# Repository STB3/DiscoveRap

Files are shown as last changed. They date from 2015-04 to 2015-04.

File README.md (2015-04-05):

# DiscoveRap
RpRap Electronics Expansion Board for the STM32F429 Discovery Board<p>
Max. 3 Extruders, X, Y, Z Axis<br>
Heated Bed<br>
Case Fan & Light<br>
Fans for each Extruder<br>
TMC260 Stepper driver<br>
USB-OTG, USB-Virtual COM, SD-Card Storage<br>
WLAN option<br>
Needs the STM32F429 Demoboard for operation<br>

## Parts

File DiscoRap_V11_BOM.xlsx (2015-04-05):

Bill of Material for DiscoRap V1.1
Qty | Value | Tolerance | Voltage | Other | Device | Package | Parts | Description | Manufacturer | Manufacturer Part No. | Mouser | Digikey
11 | Green |  |  | standard 10..20mA | LED | 0805 | LED401, LED501, LED502, LED503, LED504, LED601, LED602, LED603, LED604, LED605, LED801 | LED
6 | Molex Serie 6373 |  |  |  | M02POLAR | MOLEX-1X2 | JP704, JP706, JP709, JP710, JP711, JP902 | Molex Serie 6373 | Molex | 22-23-2021 | 538-22-23-2021
11 | Molex Serie 6373 |  |  |  | M03POLAR | MOLEX-1X3 | JP601, JP602, JP603, JP604, JP605, JP701, JP702, JP703, JP705, JP707, JP708 | Molex Serie 6373 | Molex | 22-23-2031 | 538-22-23-2031
2 |  |  |  |  | Pinheader 1x2 | RM 2.54mm | JP101, JP102 | PIN HEADER
1 |  |  |  |  | Pinheader 2x3 | RM 2.54mm | JP901 | PIN HEADER
1 |  |  |  |  | Pinheader 2x5 | RM 2.54mm | JP103 | PIN HEADER
3 |  |  |  |  | Screw Clamp 2 pol. | RM5.00 | X501, X502, X503 | Screw Clamp | Phoenix Contact | 1935161 | 651-1935161
8 |  |  |  |  | Screw Clamp 4 pol. | W237-4 | X201, X202, X203, X301, X302, X303, X401, X802 | Screw Clamp | Phoenix Contact | 1935187 | 651-1935187
0 | n.c. |  |  | not populated | Resistor | 2512 | R801 | Resistor
12 | 0R15 | 1% |  | 500mW | Resistor | 1206 | R201, R202, R203, R204, R205, R206, R301, R302, R303, R304, R305, R306 | Resistor | Panasonic | ERJ-8BSFR15V | 667-ERJ-8BSFR15V
9 | 100 | 5% |  |  | Resistor | 0805 | R402, R504, R505, R509, R603, R604, R608, R610, R614
1 | 1000uF | 20% | min. 30V |  | Electrolytic Capacitor | RM 5mm / Diameter < 11.5mm | C801 | Electrolytic Capacitor
9 | 100k | 5% |  |  | Resistor | 0805 | R401, R502, R503, R508, R601, R602, R607, R609, R613 | Resistor
7 | 100nF | 10% | min. 25V | X7R | Capacitor | 0805 | C101, C102, C103, C104, C401, C813, C814 | Capacitor
18 | 100nF |  | min. 50V | X7R | Capacitor | 0805 | C203, C204, C207, C208, C209, C211, C224, C226, C227, C303, C304, C307, C308, C309, C311, C324, C326, C327 | Capacitor
24 | 100p |  | min. 63V | NP0 | Capacitor | 0805 | C210, C212, C213, C214, C215, C216, C219, C220, C228, C229, C230, C232, C310, C312, C313, C314, C315, C316, C319, C320, C328, C329, C330, C332 | Capacitor
7 | 10k |  |  |  | Resistor | 0805 | R101, R102, R103, R104, R105, R106, R107 | Resistor
2 | 10k2 | 1% |  |  | Resistor | 0805 | R806, R808 | Resistor
1 | 10nF |  | min. 30V | X7R | Capacitor | 0805 | C809 | Capacitor
2 | 10µ | 10% | 6.3V | X5R | Capacitor | 0805 | C815, C817 | Capacitor | AVX | 08056D106KAT2A | 581-08056D106K
1 | 20k | 1% |  |  | Resistor | 0805 | R805 | Resistor
6 | 220nF | 10% | min. 16V |  | Capacitor | 0805 | C205, C206, C225, C305, C306, C325 | Capacitor
1 | 22n | 10% | min. 16V |  | Capacitor | 0805 | C812 | Capacitor
12 | 22µF | 20% | min. 35V | Ripple current >150mA | Electrolytic Capacitor | SMD B6 (6.3 x 5.3 mm²) | C217, C218, C221, C222, C231, C233, C317, C318, C321, C322, C331, C333 | Electrolytic Capacitor | KEMET | EEV226M035A9DAA | 80-EEV226M035A9DAA
1 | 8kBit serial eePROM |  |  |  | eePROM | SOT23-5L | IC102 | Serial EEPROM | Microchip | 24LC08BT-I/OT | 579-24LC08BT-I/OT
5 | 2k2 | 1% |  |  | Resistor | 0805 | R705, R710, R714, R715, R716 | Resistor
11 | 2k7 | 5% |  |  | Resistor | 0805 | R403, R501, R506, R507, R510, R605, R606, R611, R612, R615, R802 | Resistor
2 | 2n7 | 10% |  |  | Capacitor | 0805 | C802, C810 | Capacitor
1 | 2u2 | 20% | min. 16V |  | Capacitor | 0805 | C402 | Capacitor
1 | 330p | 10% |  |  | Capacitor | 0805 | C807 | Capacitor
1 | 3k24 | 1% |  |  | Resistor | 0805 | R807 | Resistor
3 | 3k3 | 5% |  |  | Resistor | 0805 | R901, R902, R903 | Resistor
1 | 3n3 | 10% |  |  | Capacitor | 0805 | C811 | Capacitor
16 | 470nF | 10% | min. 10V |  | Capacitor | 0805 | C201, C202, C223, C301, C302, C323, C701, C705, C706, C710, C711, C712, C713, C714, C715, C716 | Capacitor
1 | 47p | 10% |  |  | Capacitor | 0805 | C808 | Capacitor
6 | 4k7 | 5% |  |  | Resistor | 0805 | R701, R702, R703, R706, R707, R708 | Resistor
1 | 4k87 | 1% |  |  | Resistor | 0805 | R804 | Resistor
15 | 4n7 | 10% | min. 35V |  | Capacitor | 0805 | C403, C501, C502, C503, C601, C602, C603, C604, C605, C702, C703, C704, C707, C708, C709 | Capacitor
6 | 4µ7 | 20% | min. 25V | X5R | Capacitor | 0805 | C803, C804, C805, C806, C816, C818 | Capacitor | AVX | 08053D475MAT2A | 581-08053D475MAT2A
5 | 6k8 | 5% |  |  | Resistor | 0805 | R704, R709, R711, R712, R713 | Resistor
1 | 820 | 1% |  |  | Resistor | 0805 | R809 | Resistor
1 | 82k |  |  |  | Resistor | 0805 | R803 | Resistor
1 | AMP_1010070864 |  |  |  | AMP_1010070864 | AMP_1010070864 | X103 | Amphenol SD-Card Connector |  | 1010070864 | 523-101-00708-64
0 | n.c. |  |  | not populated | ATX-4VERTICAL | MINIFITJR-4-VERTICAL | X801
2 | B240A-13-F |  |  |  | Schottky Diode | SMA | D802, D803 | Surface Mount Schottky Power Rectifier | Diodes Inc. | B240A-13-F | 621-B240A-F
2 | BC817-25 |  |  |  | Transistor NPN | SOT23-BEC | Q101, Q102 | NPN Transistor
1 | BZX84C15 |  |  |  | Zener Diode 15V | TO236 | D801 | Zener Diode 15V | Fairchild | BZX84C15
4 | S1G-E3/5AT |  |  |  | Rectifier Diode | SMA | D401, D501, D502, D503 | Rectifier Diode | Vishay | S1G-E3/5AT | 625-S1G-E3/5AT
1 | DG2722 |  |  |  | USB Switch | MINI_QFN_10L | IC101 | USB Switch | Vishay | DG2722DN-T1-E4 | 781-DG2722DN-E4
1 | Buzzer |  | 3.3V |  | Buzzer | RM4 / RM7.6 | BUZ1 | Buzzer | Mallory | PB-09N23P-03Q | 539-PB09N23P-03Q
4 | FUSE3557 |  |  |  | Fuseholder | 3557 | F501, F801 | Fuseholder | Keystone Electronics | 3557 | 534-3557
1 | MCP1402 |  |  |  | MCP1402 | SOT23-5L | IC401 | MOSFET driver | Microchip | MCP1402T-E/OT | 579-MCP1402T-E/OT
2 | MCP23S17SO |  |  |  | MCP23S17SO | SO28W | IC103, IC104 | SPI Port Expander | Microchip | MCP23S17T-E/SO | 579-MCP23S17T-E/SO
1 | SI7145DP |  |  |  | SI7145DP | SO-8_POWERPACK | T801 | P-Ch. MOSFET 2.6mOhm -30V | Vishay | SI7145DP-T1-GE3 | 781-SI7145DP-GE3
8 | SIA400EDJ |  |  |  | SIA400EDJ | SC70-6L | T501, T502, T503, T601, T602, T603, T604, T605 | N-Ch. MOSFET 19mOhm 30V | Vishay | SIA400EDJ-T1-GE3 | 78-SIA400EDJ-T1-GE3
1 | SIR416DP |  |  |  | SIR416DP | SO-8_POWERPACK | T401 | N-Ch. MOSFET 3.8mOhm 40V | Vishay | SIR416DP-GE3 | 781-SIR416DP-GE3
1 | SRN8040-150M |  |  |  | SRN8040 | SRN8040 | L803 | Bourns Power Inductors 15uH/2.4A |  | SRN8040-150M | 652-SRN8040-150M
2 | SRN8040-220M |  |  |  | SRN8040 | SRN8040 | L801, L802 | Bourns Power Inductors 22uH/2.4A |  | SRN8040-220M | 652-SRN8040-220M
2 | Pfostenbuchse | solder side ! |  |  | 32x2 | RM 2.54mm
2 | Pfostenbuchse | solder side ! |  |  | 1x2 | RM 2.54mm
1 | TE_292303-9 |  |  |  | TE_292303-9 | TE_USB_A_SMD | X102 | TE Connectivity USB-A | TE Connectivity | 292303-9 | 571-292303-9
6 | TMC260 |  |  |  | TMC260 | SQFP-S-10X10-44 | IC201, IC202, IC203, IC301, IC302, IC303 | Stepper Driver | Trinamic | TMC260-PA-T |  | 1460-1070-1-ND
2 | TPS54332 |  |  |  | TPS54332 | PDSO-G8 | IC801, IC802 | TPS54332 | Texas Instruments | TPS54332DDAR | 595-TPS54332DDAR
1 | USB-B_SMD |  |  |  | USB-B_SMD | USB_B_SMD | X101 |  |  | KUSBEX-SMT-BS1N-BTR | 806-KUSBEXSMTBS1NBTR
 | Changes | Date | Vers. | Author
 | Initial Version | 29.03.2015 | 1.1 | DE

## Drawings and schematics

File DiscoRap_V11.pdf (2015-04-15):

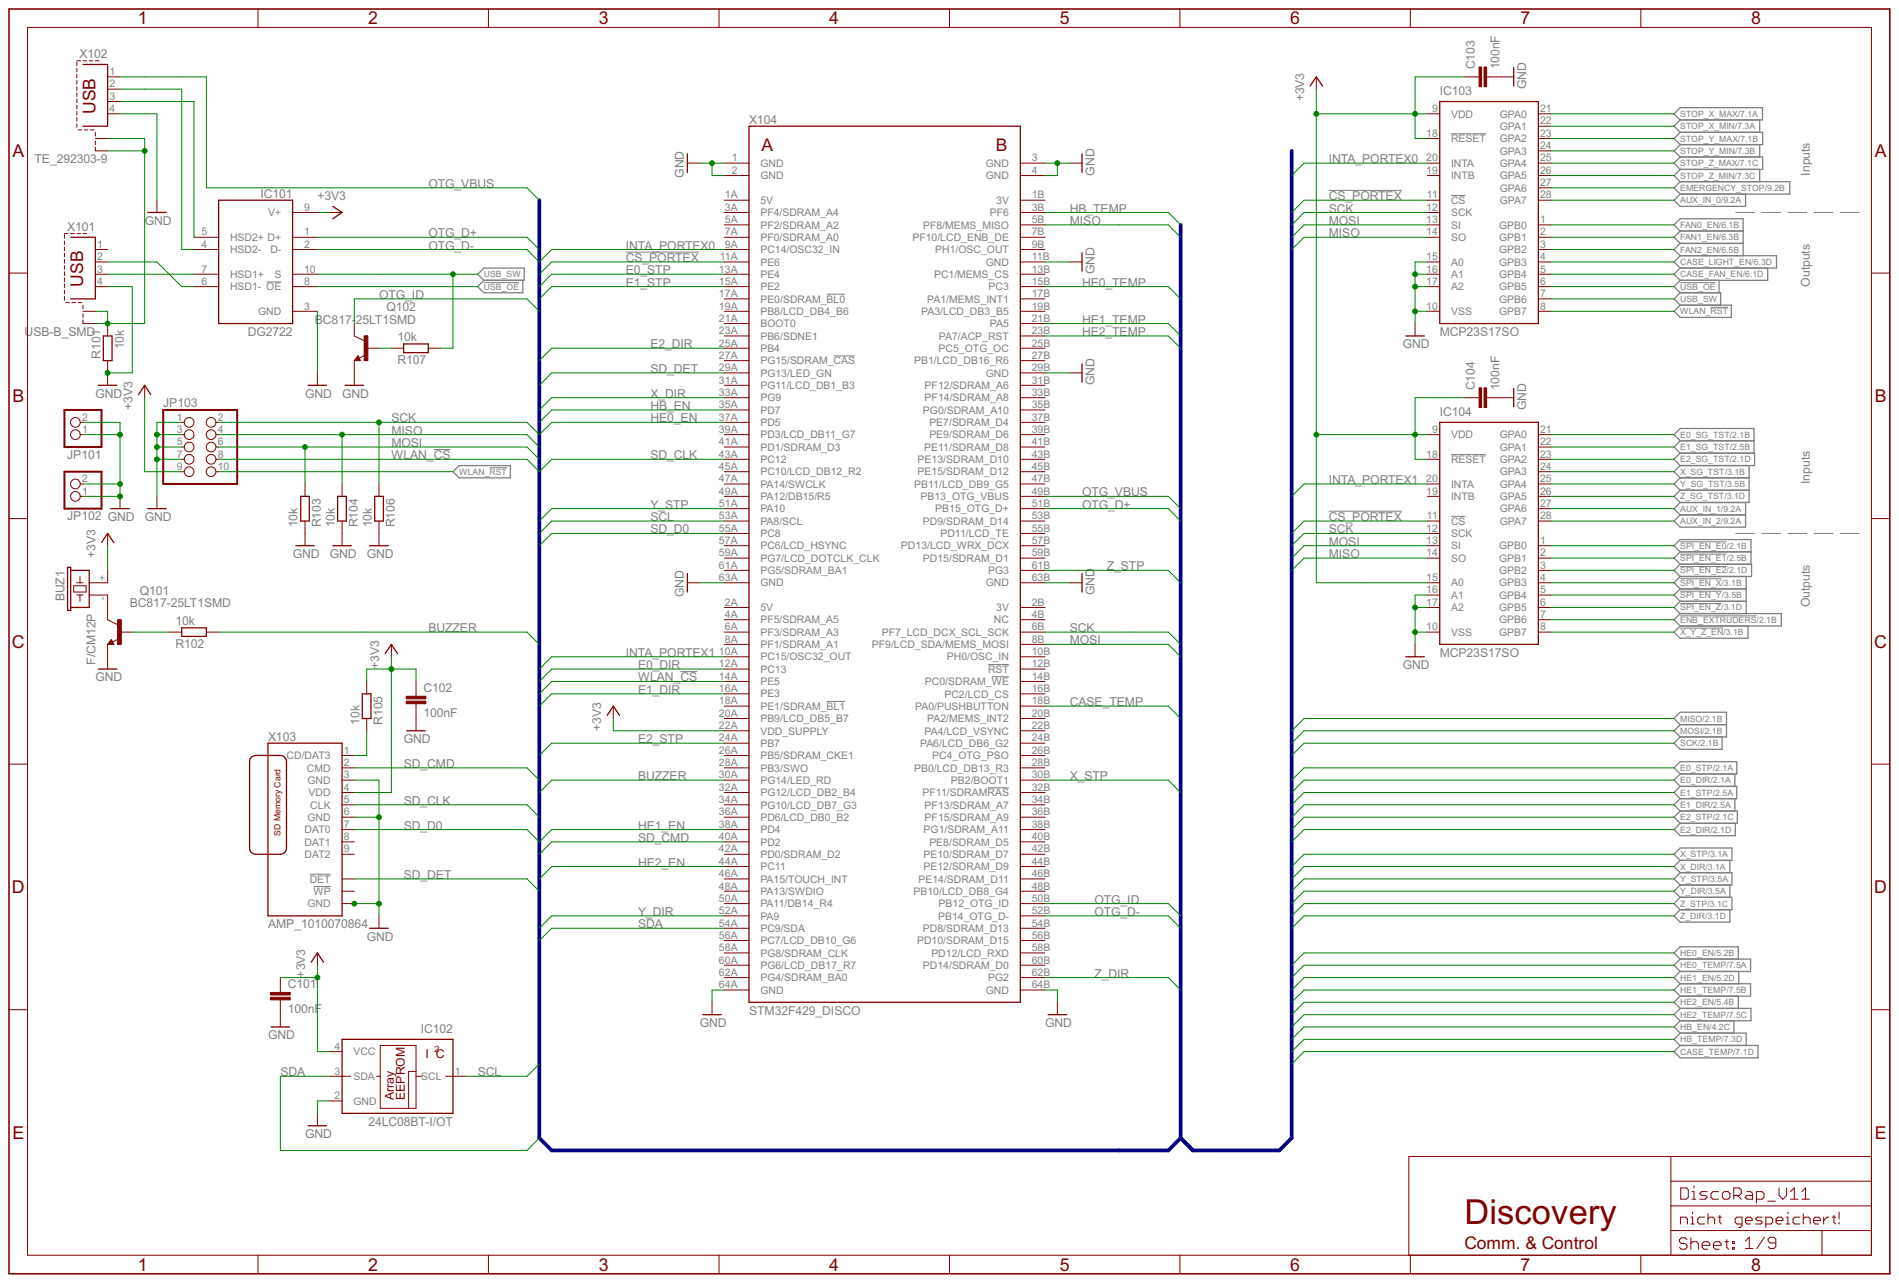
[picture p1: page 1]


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

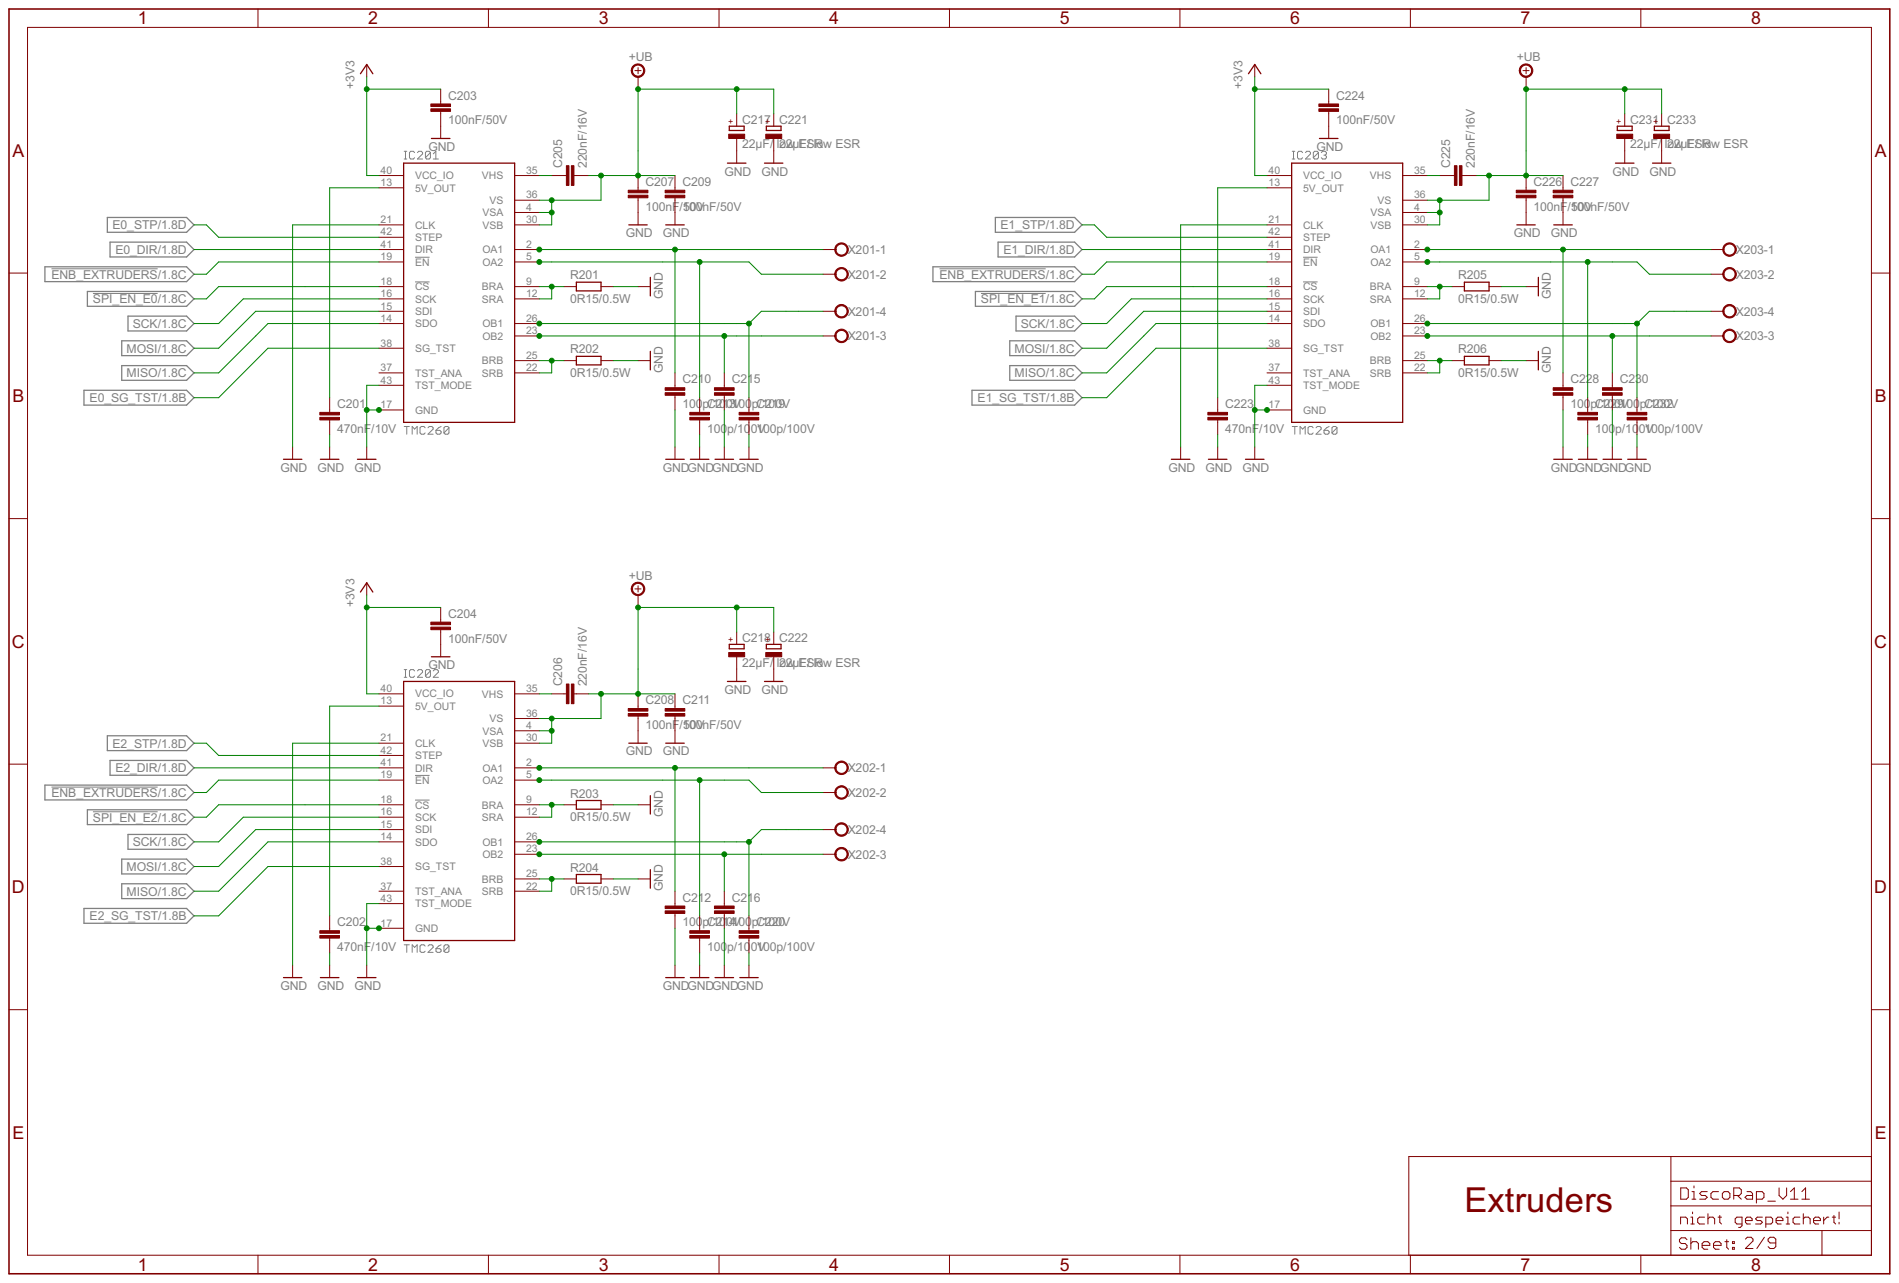
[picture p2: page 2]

22µF/ l2o2wµEFS/ lRow ESR GND GND

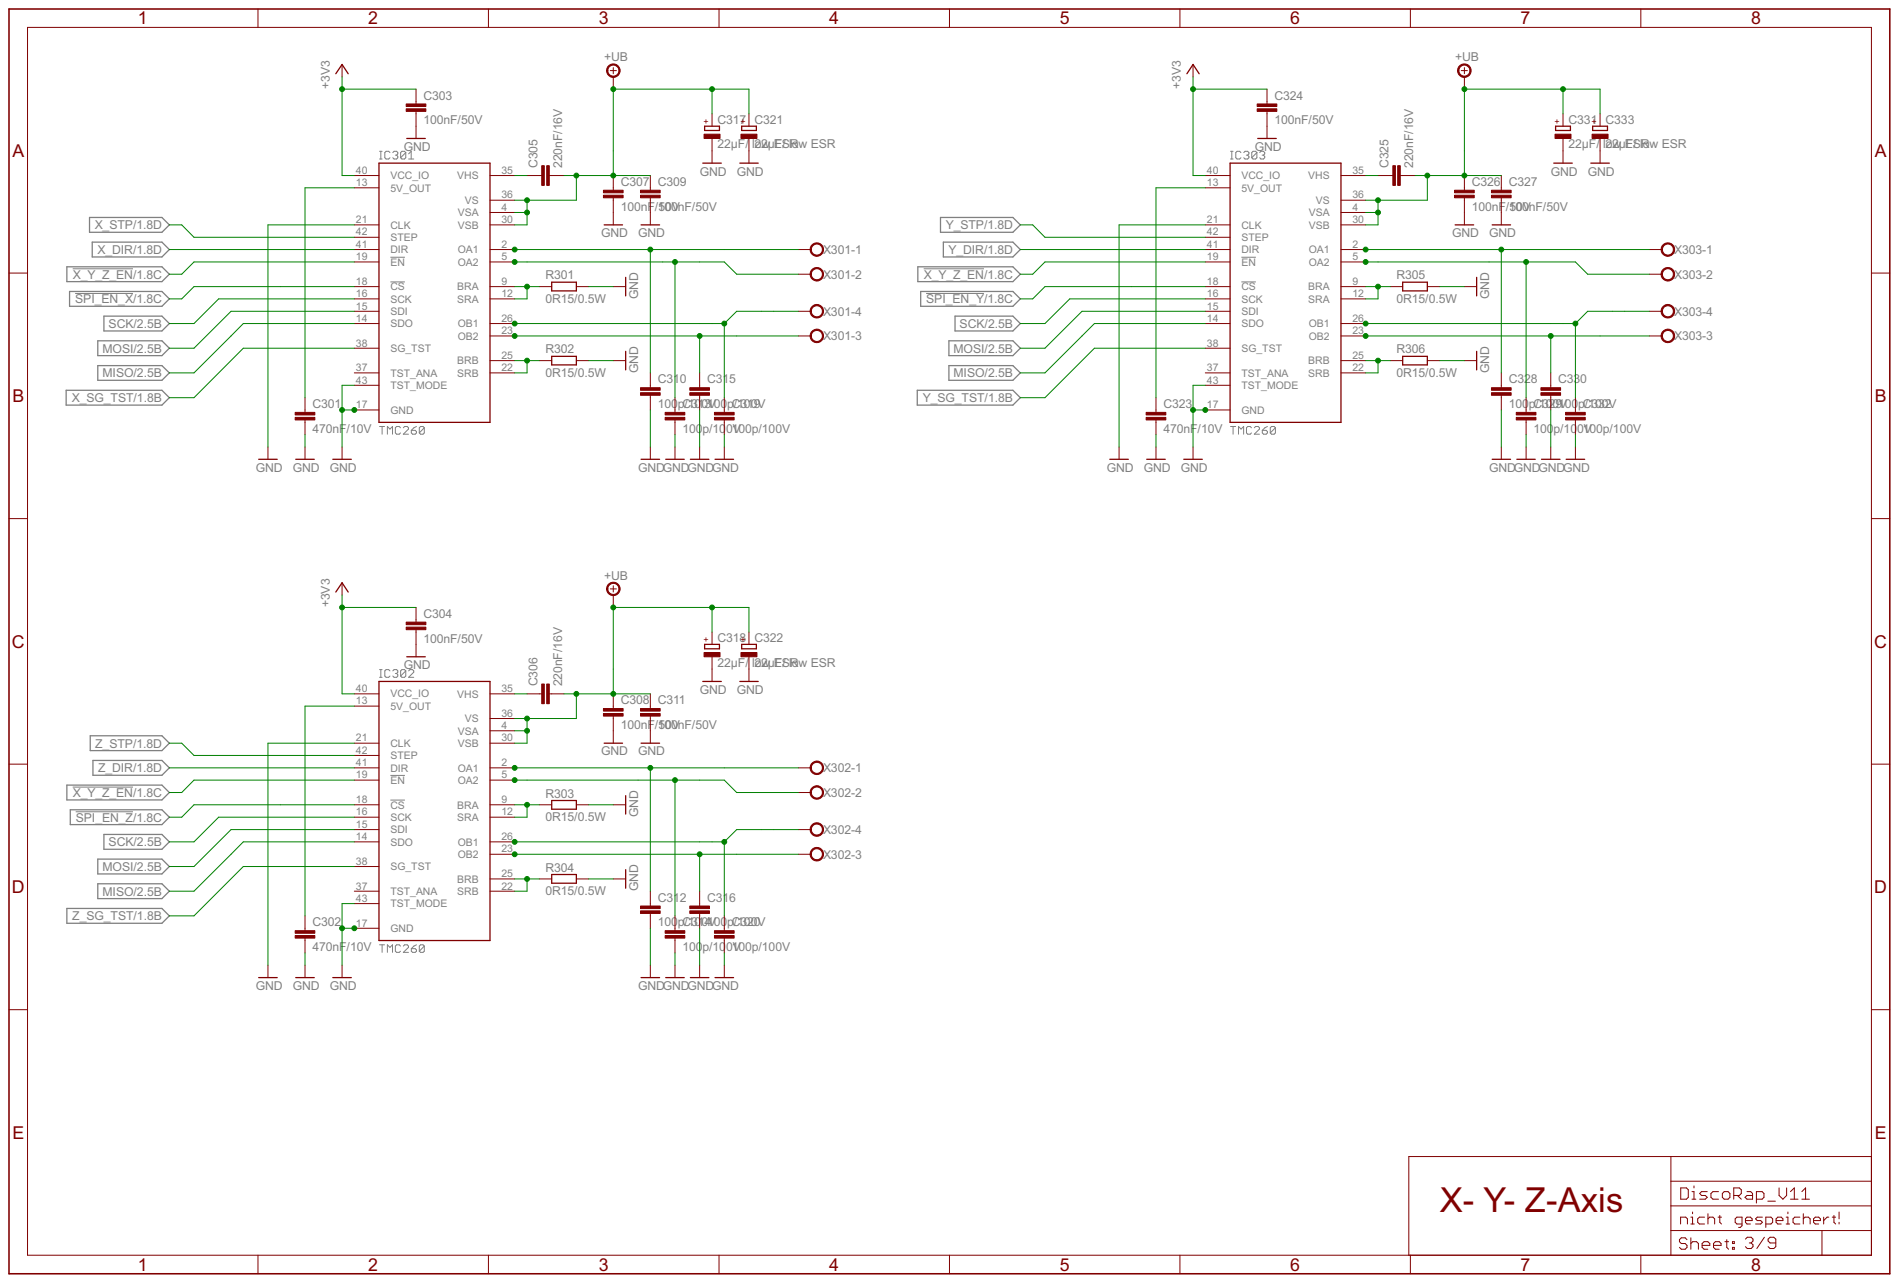
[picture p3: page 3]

22µF/ l2o2wµEFS/ lRow ESR GND GND

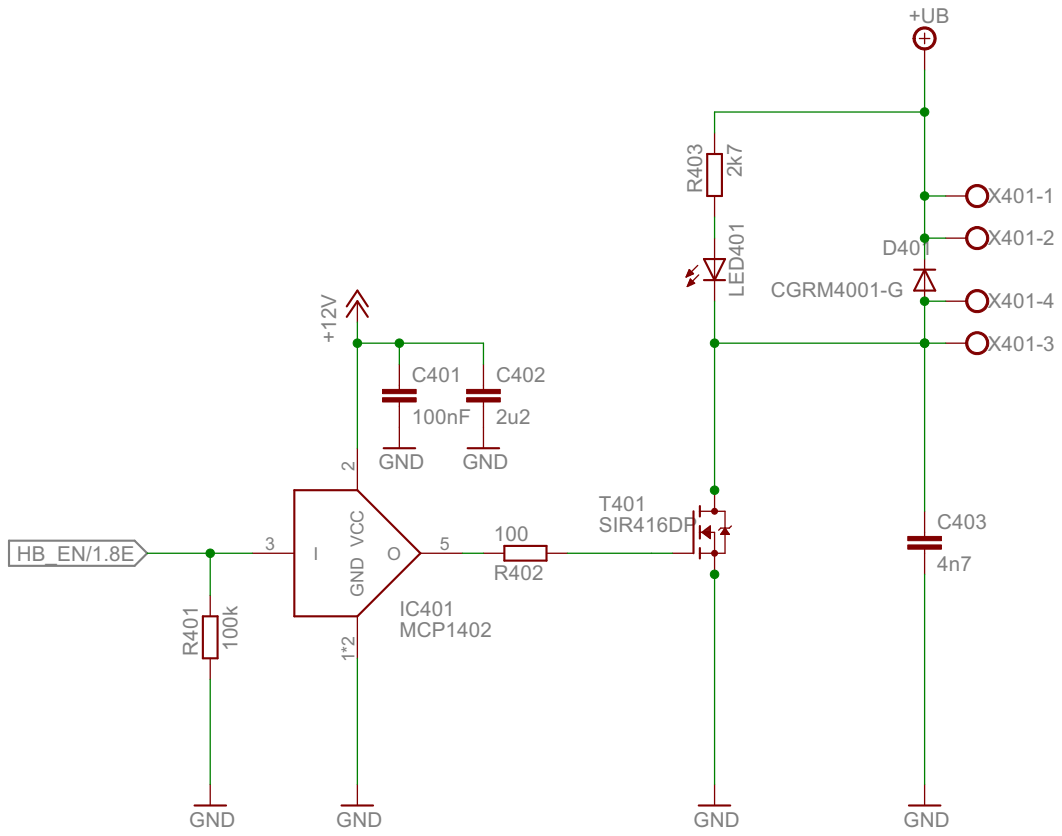
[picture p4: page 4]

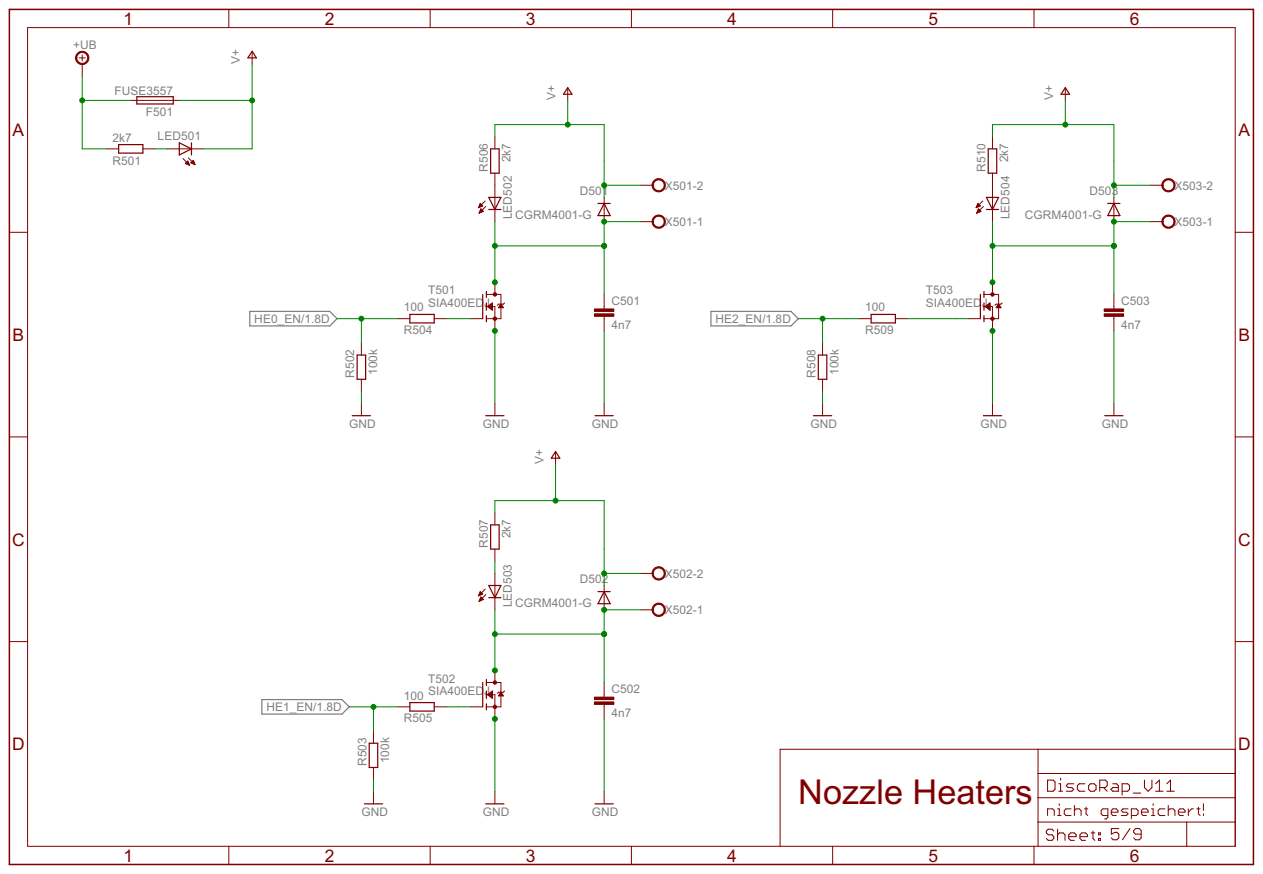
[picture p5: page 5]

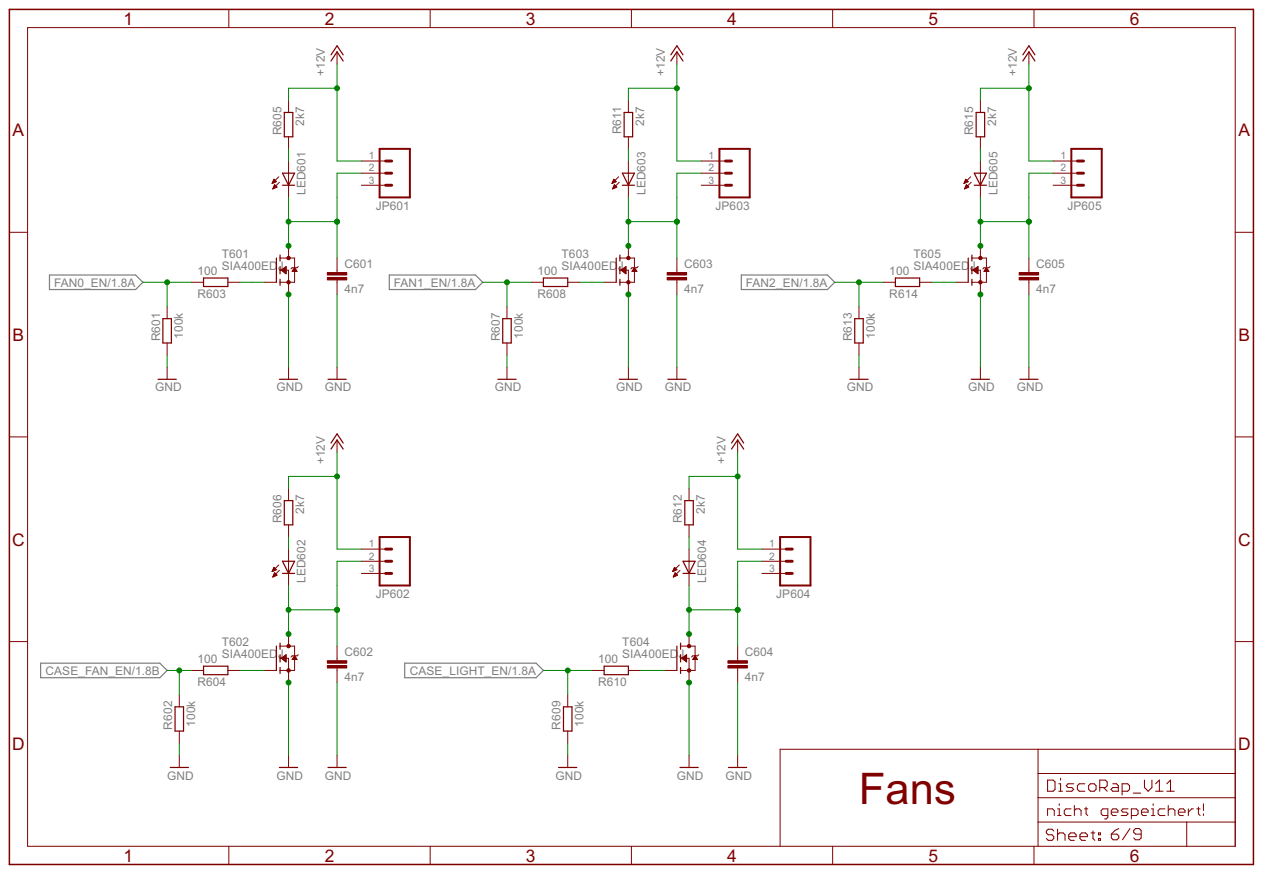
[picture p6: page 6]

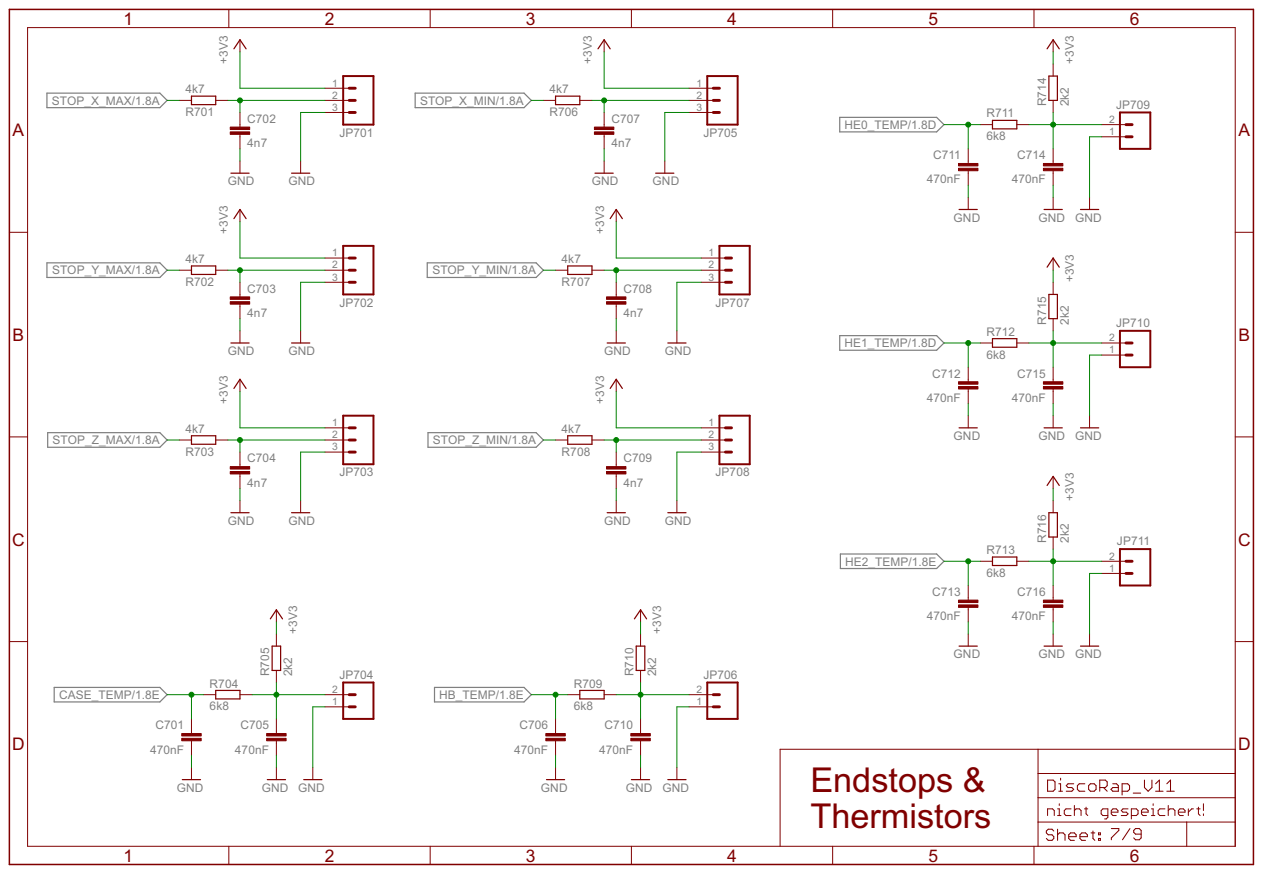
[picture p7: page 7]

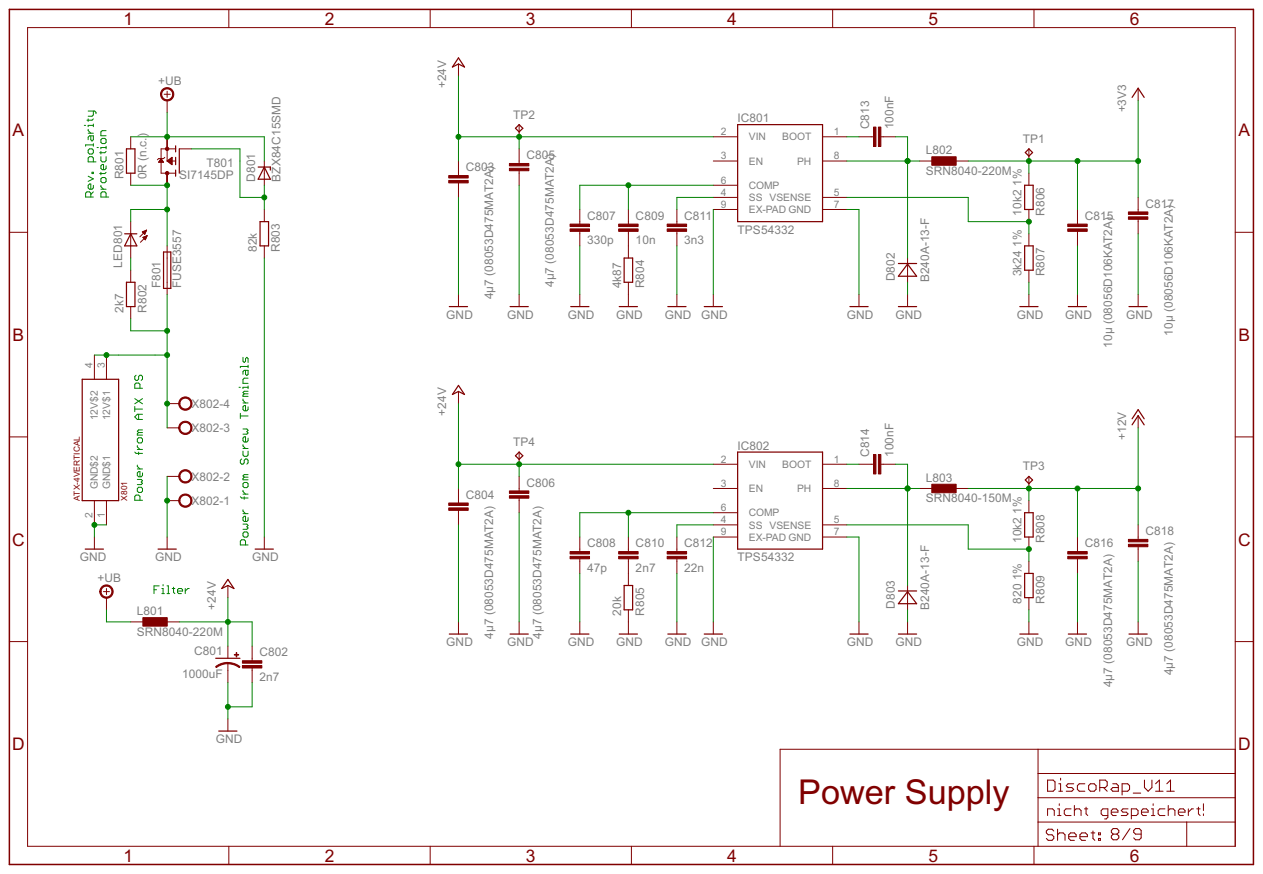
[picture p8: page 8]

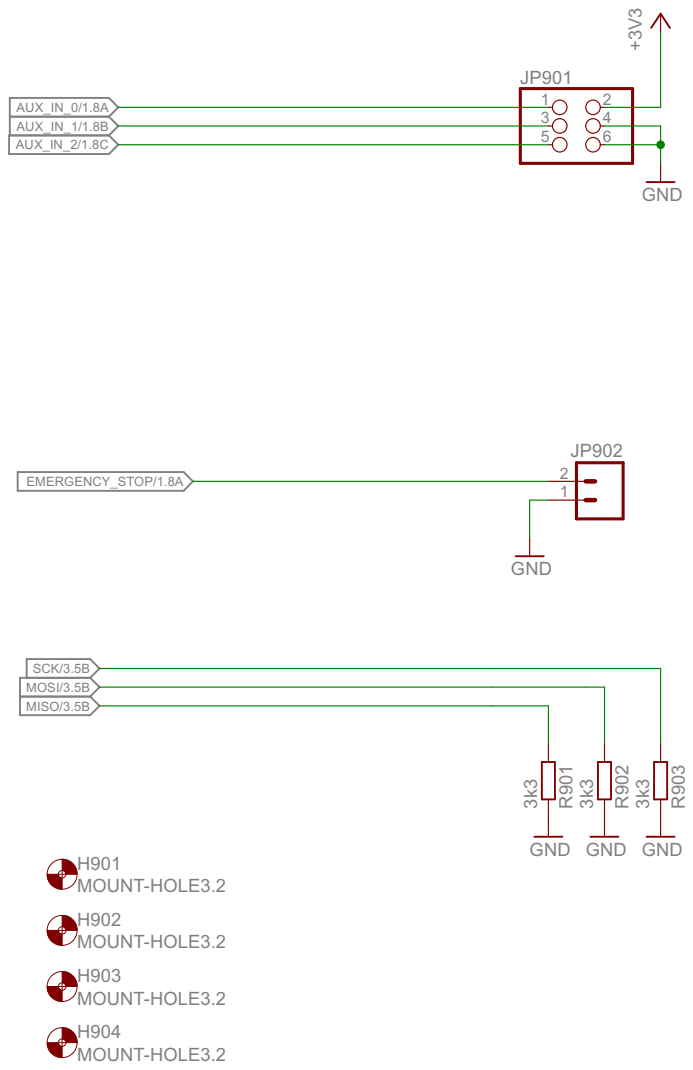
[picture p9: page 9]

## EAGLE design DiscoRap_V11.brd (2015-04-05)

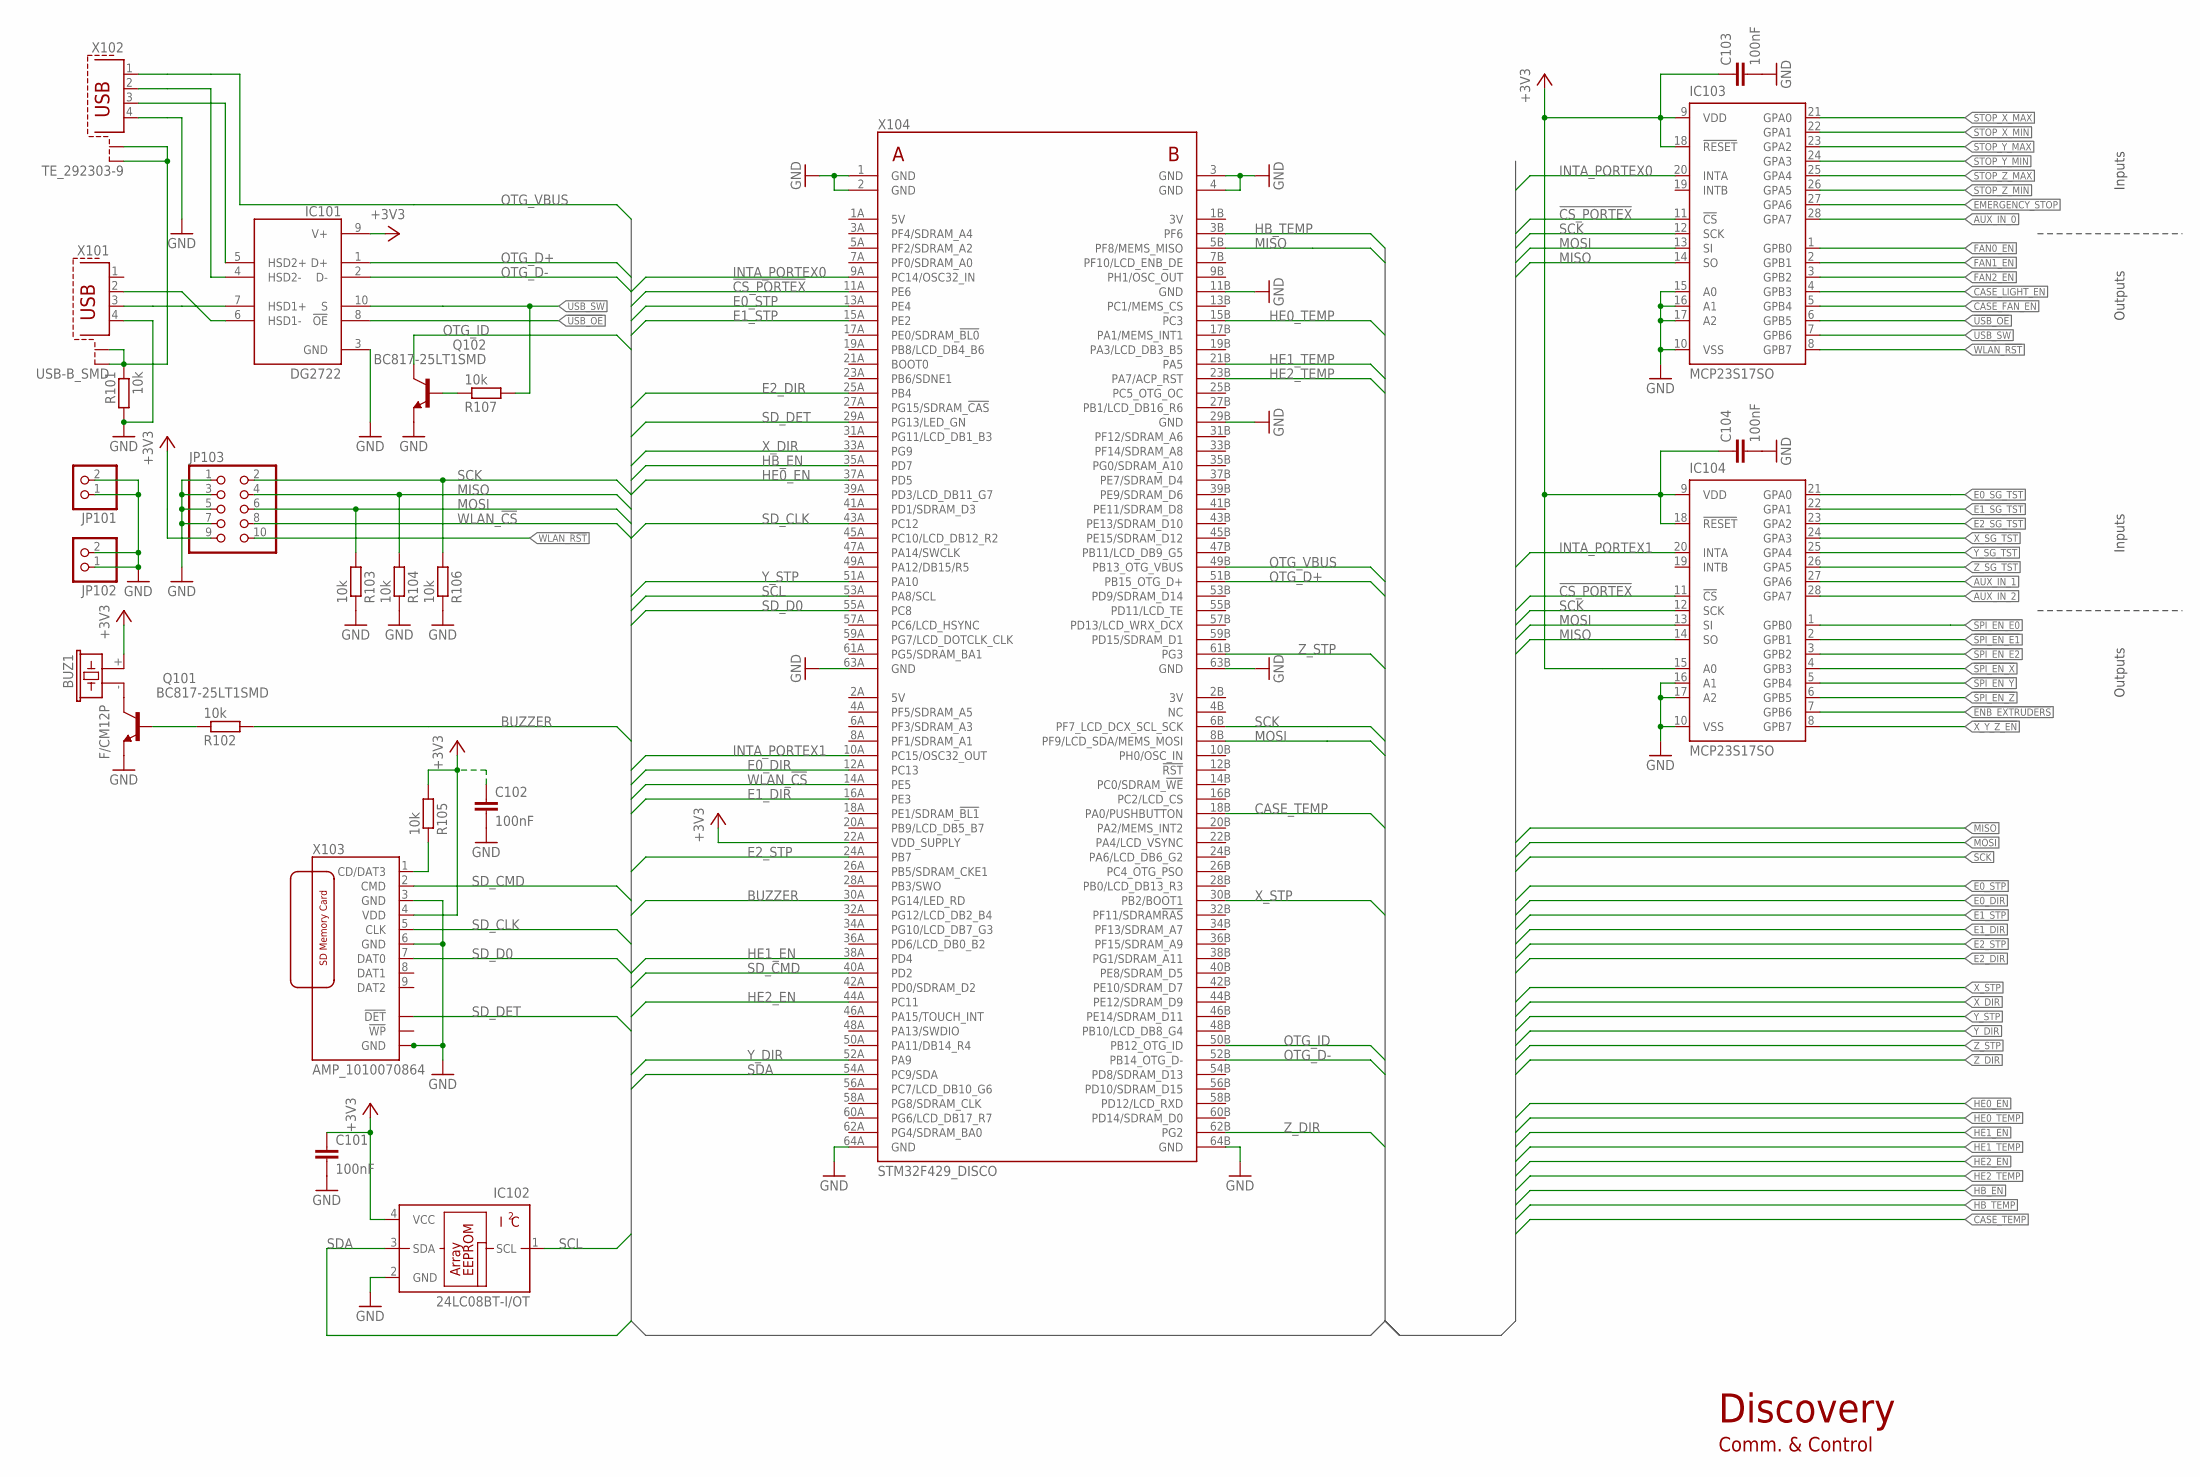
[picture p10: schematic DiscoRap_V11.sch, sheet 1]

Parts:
BUZ1: F/CM12P
C101, C102, C103, C104: 100nF; 0805
IC101: DG2722; MINI_QFN_10L
IC102: 24LC08BT-I/OT; SOT23-5L
IC103, IC104: MCP23S17SO; SO28W
JP101, JP102: PINHD-1X2; 1X02
JP103: PINHD-2X5; 2X05
Q101, Q102: BC817-25LT1SMD; SOT23-BEC
R101, R102, R103, R104, R105, R106, R107: 10k; 0805
X101: USB-B_SMD; USB_B_SMD
X102: TE_292303-9; TE_USB_A_SMD
X103: AMP_1010070864
X104: STM32F429_DISCO; STM429_DISCOVERY

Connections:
!CS_PORTEX: IC103.11 (!CS), IC104.11 (!CS), X104.11A (PE6)
!ENB_EXTRUDERS: IC104.7 (GPB6); also elsewhere on the board
!SPI_EN_E0: IC104.1 (GPB0); also elsewhere on the board
!SPI_EN_E1: IC104.2 (GPB1); also elsewhere on the board
!SPI_EN_E2: IC104.3 (GPB2); also elsewhere on the board
!SPI_EN_X: IC104.4 (GPB3); also elsewhere on the board
!SPI_EN_Y: IC104.5 (GPB4); also elsewhere on the board
!SPI_EN_Z: IC104.6 (GPB5); also elsewhere on the board
!USB_OE: IC101.8 (!OE), IC103.6 (GPB5)
!X_Y_Z_EN: IC104.8 (GPB7); also elsewhere on the board
+3V3: BUZ1.+ (1), C101.1, C102.1, C103.1, C104.1, IC101.9 (V+), IC102.4 (VCC), IC103.9 (VDD), IC103.18 (!RESET), IC104.9 (VDD), IC104.15 (A0), IC104.18 (!RESET), JP103.9, R105.2, X103.4 (VDD), X104.22A (VDD_SUPPLY); also elsewhere on the board
AUX_IN_0: IC103.28 (GPA7); also elsewhere on the board
AUX_IN_1: IC104.27 (GPA6); also elsewhere on the board
AUX_IN_2: IC104.28 (GPA7); also elsewhere on the board
BUZZER: R102.2, X104.30A (PG14/LED_RD)
CASE_FAN_EN: IC103.5 (GPB4); also elsewhere on the board
CASE_LIGHT_EN: IC103.4 (GPB3); also elsewhere on the board
CASE_TEMP: X104.18B (PA0/PUSHBUTTON); also elsewhere on the board
E0_DIR: X104.12A (PC13); also elsewhere on the board
E0_SG_TST: IC104.21 (GPA0); also elsewhere on the board
E0_STP: X104.13A (PE4); also elsewhere on the board
E1_DIR: X104.16A (PE3); also elsewhere on the board
E1_SG_TST: IC104.22 (GPA1); also elsewhere on the board
E1_STP: X104.15A (PE2); also elsewhere on the board
E2_DIR: X104.25A (PB4); also elsewhere on the board
E2_SG_TST: IC104.23 (GPA2); also elsewhere on the board
E2_STP: X104.24A (PB7); also elsewhere on the board
EMERGENCY_STOP: IC103.27 (GPA6); also elsewhere on the board
FAN0_EN: IC103.1 (GPB0); also elsewhere on the board
FAN1_EN: IC103.2 (GPB1); also elsewhere on the board
FAN2_EN: IC103.3 (GPB2); also elsewhere on the board
GND: C101.2, C102.2, C103.2, C104.2, IC101.3 (GND), IC102.2 (GND), IC103.10 (VSS), IC103.15 (A0), IC103.16 (A1), IC103.17 (A2), IC104.10 (VSS), IC104.16 (A1), IC104.17 (A2), JP101.1, JP101.2, JP102.1, JP102.2, JP103.1, JP103.3, JP103.5, JP103.7, Q101.E, Q102.E, R101.2, R103.1, R104.1, R106.1, X101.4, X102.4, X103.3 (GND), X103.6 (GND), X103.GND1 (GND), X103.GND2 (GND), X103.GND3 (GND), X103.GND4 (GND), X104.1 (GND), X104.2 (GND), X104.3 (GND), X104.4 (GND), X104.11B (GND), X104.29B (GND), X104.63A (GND), X104.63B (GND), X104.64A (GND), X104.64B (GND); also elsewhere on the board
HB_EN: X104.35A (PD7); also elsewhere on the board
HB_TEMP: X104.3B (PF6); also elsewhere on the board
HE0_EN: X104.37A (PD5); also elsewhere on the board
HE0_TEMP: X104.15B (PC3); also elsewhere on the board
HE1_EN: X104.38A (PD4); also elsewhere on the board
HE1_TEMP: X104.21B (PA5); also elsewhere on the board
HE2_EN: X104.44A (PC11); also elsewhere on the board
HE2_TEMP: X104.23B (PA7/ACP_RST); also elsewhere on the board
INTA_PORTEX0: IC103.20 (INTA), X104.9A (PC14/OSC32_IN)
INTA_PORTEX1: IC104.20 (INTA), X104.10A (PC15/OSC32_OUT)
MISO: IC103.14 (SO), IC104.14 (SO), JP103.4, R104.2, X104.5B (PF8/MEMS_MISO); also elsewhere on the board
MOSI: IC103.13 (SI), IC104.13 (SI), JP103.6, R103.2, X104.8B (PF9/LCD_SDA/MEMS_MOSI); also elsewhere on the board
unnamed: R105.1, X103.1 (CD/DAT3)
unnamed: IC101.4 (HSD2-), X102.2
unnamed: IC101.5 (HSD2+), X102.3
unnamed: IC101.7 (HSD1+), X101.3
unnamed: BUZ1.- (2), Q101.C
unnamed: IC101.6 (HSD1-), X101.2
unnamed: R101.1, X101.5 (S1), X101.6 (S2), X102.5 (S1), X102.6 (S2)
unnamed: Q102.B, R107.1
unnamed: Q101.B, R102.1
OTG_D+: IC101.1 (D+), X104.51B (PB15_OTG_D+)
OTG_D-: IC101.2 (D-), X104.52B (PB14_OTG_D-)
OTG_ID: Q102.C, X104.50B (PB12_OTG_ID)
OTG_VBUS: X102.1, X104.49B (PB13_OTG_VBUS)
SCK: IC103.12 (SCK), IC104.12 (SCK), JP103.2, R106.2, X104.6B (PF7_LCD_DCX_SCL_SCK); also elsewhere on the board
SCL: IC102.1 (SCL), X104.53A (PA8/SCL)
SDA: IC102.3 (SDA), X104.54A (PC9/SDA)
SD_CLK: X103.5 (CLK), X104.43A (PC12)
SD_CMD: X103.2 (CMD), X104.40A (PD2)
SD_D0: X103.7 (DAT0), X104.55A (PC8)
SD_DET: X103.DET (!DET), X104.29A (PG13/LED_GN)
STOP_X_MAX: IC103.21 (GPA0); also elsewhere on the board
STOP_X_MIN: IC103.22 (GPA1); also elsewhere on the board
STOP_Y_MAX: IC103.23 (GPA2); also elsewhere on the board
STOP_Y_MIN: IC103.24 (GPA3); also elsewhere on the board
STOP_Z_MAX: IC103.25 (GPA4); also elsewhere on the board
STOP_Z_MIN: IC103.26 (GPA5); also elsewhere on the board
USB_SW: IC101.10 (S), IC103.7 (GPB6), R107.2
WLAN_!CS: JP103.8, X104.14A (PE5)
WLAN_!RST: IC103.8 (GPB7), JP103.10
X_DIR: X104.33A (PG9); also elsewhere on the board
X_SG_TST: IC104.24 (GPA3); also elsewhere on the board
X_STP: X104.30B (PB2/BOOT1); also elsewhere on the board
Y_DIR: X104.52A (PA9); also elsewhere on the board
Y_SG_TST: IC104.25 (GPA4); also elsewhere on the board
Y_STP: X104.51A (PA10); also elsewhere on the board
Z_DIR: X104.62B (PG2); also elsewhere on the board
Z_SG_TST: IC104.26 (GPA5); also elsewhere on the board
Z_STP: X104.61B (PG3); also elsewhere on the board

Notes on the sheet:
Inputs
Outputs
Discovery
Comm. & Control

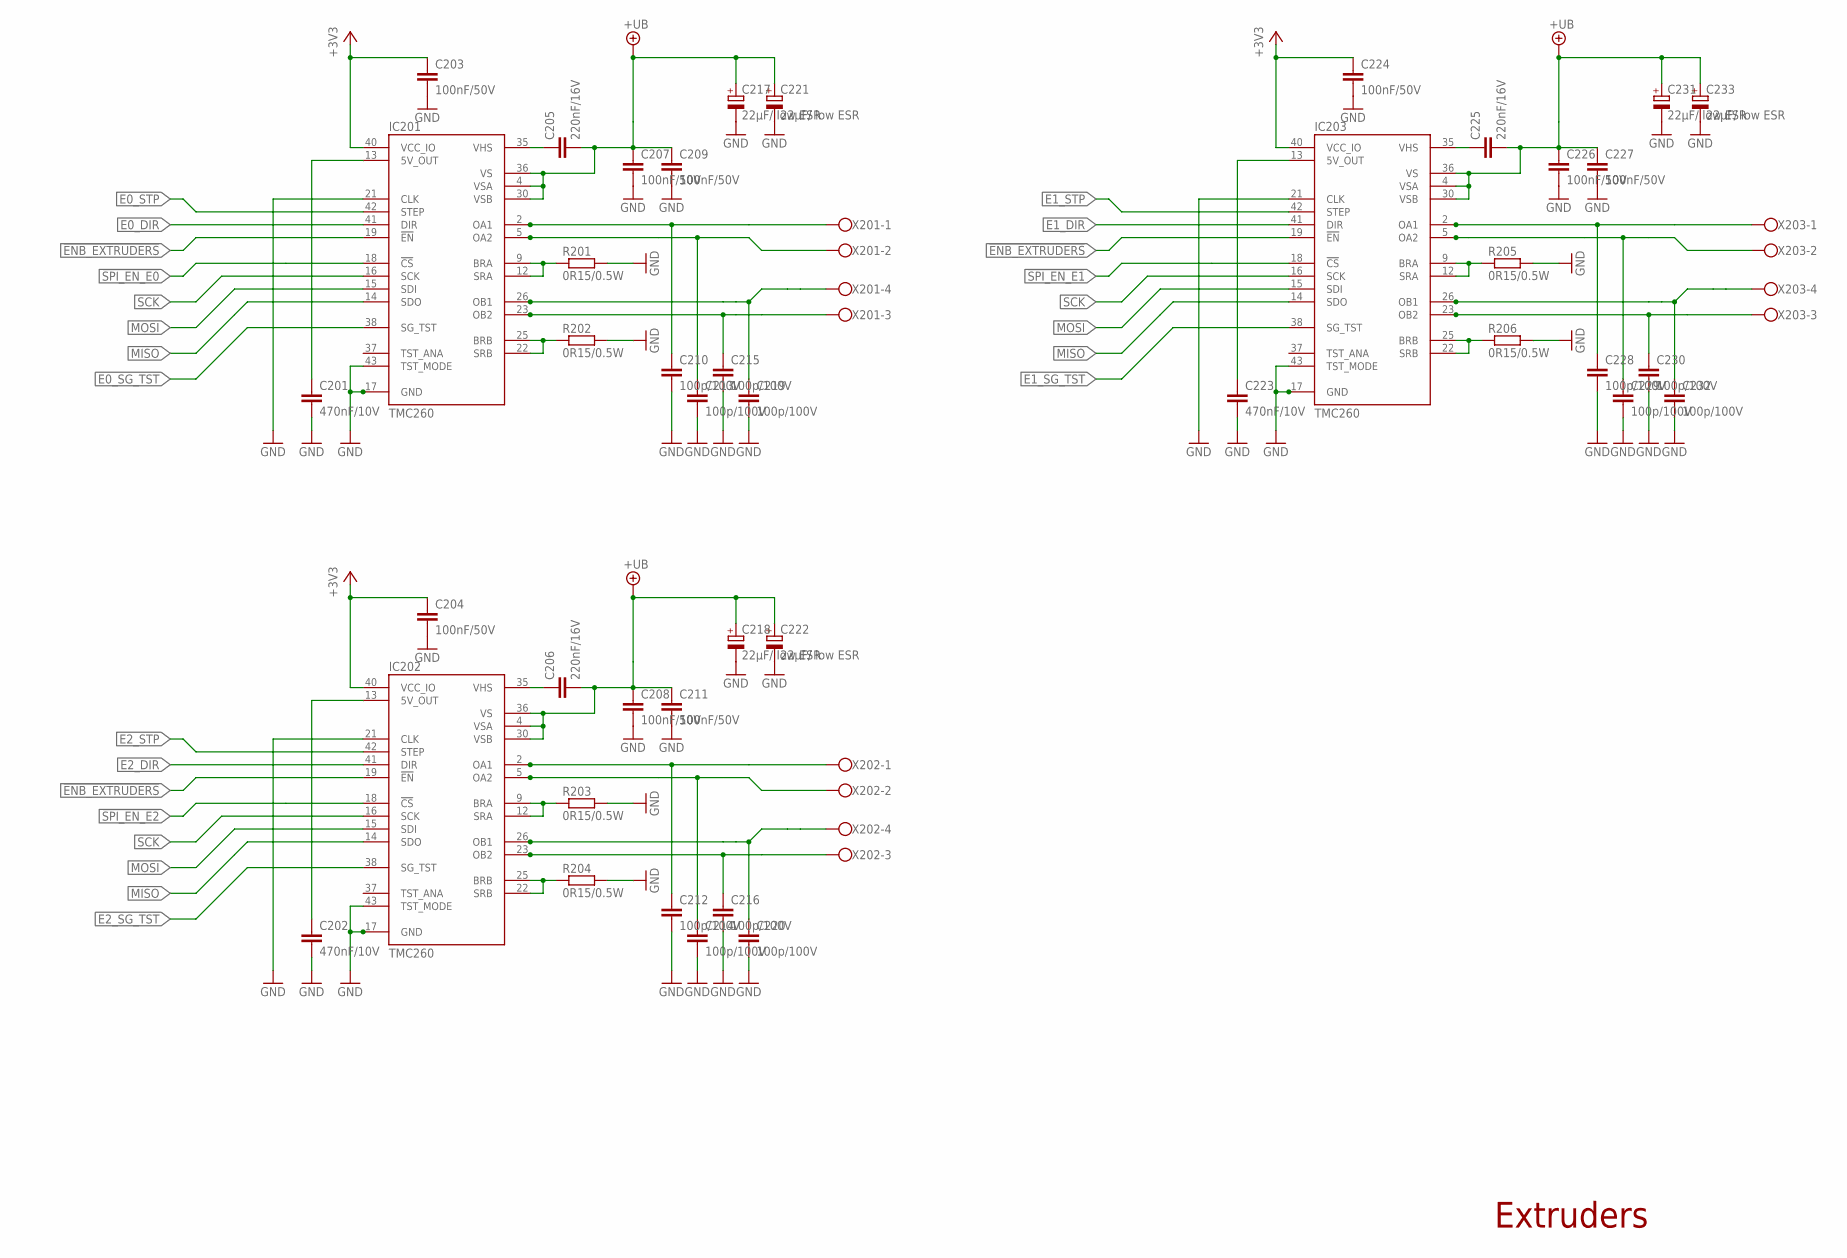
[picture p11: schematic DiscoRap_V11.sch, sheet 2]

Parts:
C201, C202, C223: 470nF/10V; 0805
C203, C204, C207, C208, C209, C211, C224, C226, C227: 100nF/50V; 0805
C205, C206, C225: 220nF/16V; 0805
C210, C212, C213, C214, C215, C216, C219, C220, C228, C229, C230, C232: 100p/100V; 0805
C217, C218, C221, C222, C231, C233: 22µF/ low ESR; SANYO-OSCON_SMD_B6
IC201, IC202, IC203: TMC260; SQFP-S-10X10-44
R201, R202, R203, R204, R205, R206: 0R15/0.5W; R1206
X201, X202, X203: W237-4

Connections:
!ENB_EXTRUDERS: IC201.19 (!EN), IC202.19 (!EN), IC203.19 (!EN); also elsewhere on the board
!SPI_EN_E0: IC201.18 (!CS); also elsewhere on the board
!SPI_EN_E1: IC203.18 (!CS); also elsewhere on the board
!SPI_EN_E2: IC202.18 (!CS); also elsewhere on the board
+3V3: C203.1, C204.1, C224.1, IC201.40 (VCC_IO), IC202.40 (VCC_IO), IC203.40 (VCC_IO); also elsewhere on the board
+UB: C205.2, C206.2, C207.1, C208.1, C209.1, C211.1, C217.+, C218.+, C221.+, C222.+, C225.2, C226.1, C227.1, C231.+, C233.+, IC201.4 (VSA), IC201.30 (VSB), IC201.36 (VS), IC202.4 (VSA), IC202.30 (VSB), IC202.36 (VS), IC203.4 (VSA), IC203.30 (VSB), IC203.36 (VS); also elsewhere on the board
E0_A1: C210.1, IC201.2 (OA1), IC201.3 (OA1), IC201.7 (OA1), IC201.8 (OA1), X201.1
E0_A2: C213.1, IC201.5 (OA2), IC201.6 (OA2), IC201.10 (OA2), IC201.11 (OA2), X201.2
E0_A3: C229.1, IC203.5 (OA2), IC203.6 (OA2), IC203.10 (OA2), IC203.11 (OA2), X203.2
E0_A4: C228.1, IC203.2 (OA1), IC203.3 (OA1), IC203.7 (OA1), IC203.8 (OA1), X203.1
E0_A5: C214.1, IC202.5 (OA2), IC202.6 (OA2), IC202.10 (OA2), IC202.11 (OA2), X202.2
E0_A6: C212.1, IC202.2 (OA1), IC202.3 (OA1), IC202.7 (OA1), IC202.8 (OA1), X202.1
E0_B1: C219.1, IC201.26 (OB1), IC201.27 (OB1), IC201.31 (OB1), IC201.32 (OB1), X201.4
E0_B2: C215.1, IC201.23 (OB2), IC201.24 (OB2), IC201.28 (OB2), IC201.29 (OB2), X201.3
E0_B3: C232.1, IC203.26 (OB1), IC203.27 (OB1), IC203.31 (OB1), IC203.32 (OB1), X203.4
E0_B4: C230.1, IC203.23 (OB2), IC203.24 (OB2), IC203.28 (OB2), IC203.29 (OB2), X203.3
E0_B5: C220.1, IC202.26 (OB1), IC202.27 (OB1), IC202.31 (OB1), IC202.32 (OB1), X202.4
E0_B6: C216.1, IC202.23 (OB2), IC202.24 (OB2), IC202.28 (OB2), IC202.29 (OB2), X202.3
E0_DIR: IC201.41 (DIR); also elsewhere on the board
E0_SG_TST: IC201.38 (SG_TST); also elsewhere on the board
E0_STP: IC201.42 (STEP); also elsewhere on the board
E1_DIR: IC203.41 (DIR); also elsewhere on the board
E1_SG_TST: IC203.38 (SG_TST); also elsewhere on the board
E1_STP: IC203.42 (STEP); also elsewhere on the board
E2_DIR: IC202.41 (DIR); also elsewhere on the board
E2_SG_TST: IC202.38 (SG_TST); also elsewhere on the board
E2_STP: IC202.42 (STEP); also elsewhere on the board
GND: C201.2, C202.2, C203.2, C204.2, C207.2, C208.2, C209.2, C210.2, C211.2, C212.2, C213.2, C214.2, C215.2, C216.2, C217.-, C218.-, C219.2, C220.2, C221.-, C222.-, C223.2, C224.2, C226.2, C227.2, C228.2, C229.2, C230.2, C231.-, C232.2, C233.-, IC201.17 (GND), IC201.21 (CLK), IC201.39 (GND), IC201.43 (TST_MODE), IC201.44 (GND), IC202.17 (GND), IC202.21 (CLK), IC202.39 (GND), IC202.43 (TST_MODE), IC202.44 (GND), IC203.17 (GND), IC203.21 (CLK), IC203.39 (GND), IC203.43 (TST_MODE), IC203.44 (GND), R201.2, R202.2, R203.2, R204.2, R205.2, R206.2; also elsewhere on the board
MISO: IC201.14 (SDO), IC202.14 (SDO), IC203.14 (SDO); also elsewhere on the board
MOSI: IC201.15 (SDI), IC202.15 (SDI), IC203.15 (SDI); also elsewhere on the board
unnamed: C205.1, IC201.35 (VHS)
unnamed: IC201.9 (BRA), IC201.12 (SRA), R201.1
unnamed: IC201.22 (SRB), IC201.25 (BRB), R202.1
unnamed: C201.1, IC201.13 (5V_OUT)
unnamed: C225.1, IC203.35 (VHS)
unnamed: IC203.9 (BRA), IC203.12 (SRA), R205.1
unnamed: IC203.22 (SRB), IC203.25 (BRB), R206.1
unnamed: C223.1, IC203.13 (5V_OUT)
unnamed: C206.1, IC202.35 (VHS)
unnamed: IC202.9 (BRA), IC202.12 (SRA), R203.1
unnamed: IC202.22 (SRB), IC202.25 (BRB), R204.1
unnamed: C202.1, IC202.13 (5V_OUT)
SCK: IC201.16 (SCK), IC202.16 (SCK), IC203.16 (SCK); also elsewhere on the board

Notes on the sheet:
Extruders

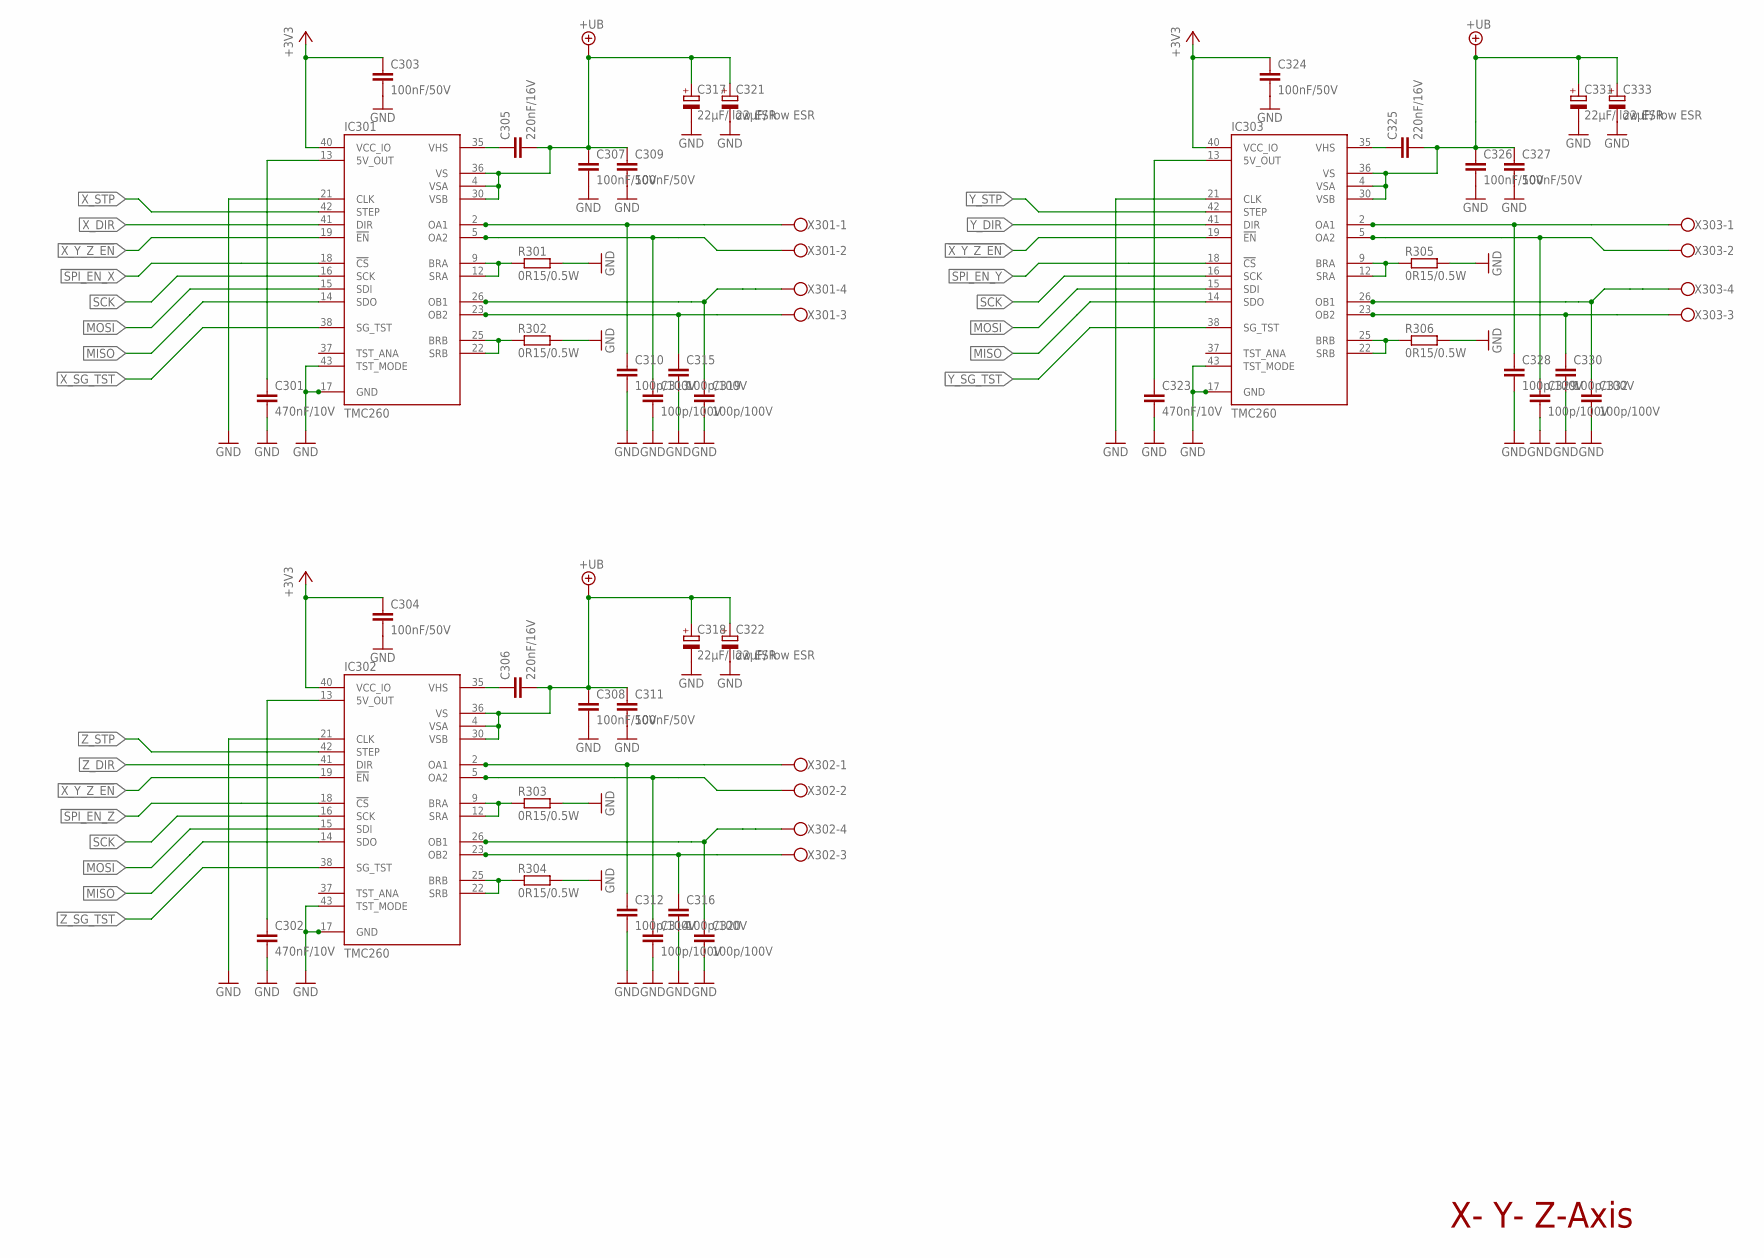
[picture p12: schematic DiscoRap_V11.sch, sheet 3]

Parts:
C301, C302, C323: 470nF/10V; 0805
C303, C304, C307, C308, C309, C311, C324, C326, C327: 100nF/50V; 0805
C305, C306, C325: 220nF/16V; 0805
C310, C312, C313, C314, C315, C316, C319, C320, C328, C329, C330, C332: 100p/100V; 0805
C317, C318, C321, C322, C331, C333: 22µF/ low ESR; SANYO-OSCON_SMD_B6
IC301, IC302, IC303: TMC260; SQFP-S-10X10-44
R301, R302, R303, R304, R305, R306: 0R15/0.5W; R1206
X301, X302, X303: W237-4

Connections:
!SPI_EN_X: IC301.18 (!CS); also elsewhere on the board
!SPI_EN_Y: IC303.18 (!CS); also elsewhere on the board
!SPI_EN_Z: IC302.18 (!CS); also elsewhere on the board
!X_Y_Z_EN: IC301.19 (!EN), IC302.19 (!EN), IC303.19 (!EN); also elsewhere on the board
+3V3: C303.1, C304.1, C324.1, IC301.40 (VCC_IO), IC302.40 (VCC_IO), IC303.40 (VCC_IO); also elsewhere on the board
+UB: C305.2, C306.2, C307.1, C308.1, C309.1, C311.1, C317.+, C318.+, C321.+, C322.+, C325.2, C326.1, C327.1, C331.+, C333.+, IC301.4 (VSA), IC301.30 (VSB), IC301.36 (VS), IC302.4 (VSA), IC302.30 (VSB), IC302.36 (VS), IC303.4 (VSA), IC303.30 (VSB), IC303.36 (VS); also elsewhere on the board
E0_A7: C313.1, IC301.5 (OA2), IC301.6 (OA2), IC301.10 (OA2), IC301.11 (OA2), X301.2
E0_A8: C310.1, IC301.2 (OA1), IC301.3 (OA1), IC301.7 (OA1), IC301.8 (OA1), X301.1
E0_A9: C329.1, IC303.5 (OA2), IC303.6 (OA2), IC303.10 (OA2), IC303.11 (OA2), X303.2
E0_A10: C328.1, IC303.2 (OA1), IC303.3 (OA1), IC303.7 (OA1), IC303.8 (OA1), X303.1
E0_A11: C314.1, IC302.5 (OA2), IC302.6 (OA2), IC302.10 (OA2), IC302.11 (OA2), X302.2
E0_A12: C312.1, IC302.2 (OA1), IC302.3 (OA1), IC302.7 (OA1), IC302.8 (OA1), X302.1
E0_B7: C319.1, IC301.26 (OB1), IC301.27 (OB1), IC301.31 (OB1), IC301.32 (OB1), X301.4
E0_B8: C315.1, IC301.23 (OB2), IC301.24 (OB2), IC301.28 (OB2), IC301.29 (OB2), X301.3
E0_B9: C332.1, IC303.26 (OB1), IC303.27 (OB1), IC303.31 (OB1), IC303.32 (OB1), X303.4
E0_B10: C330.1, IC303.23 (OB2), IC303.24 (OB2), IC303.28 (OB2), IC303.29 (OB2), X303.3
E0_B11: C320.1, IC302.26 (OB1), IC302.27 (OB1), IC302.31 (OB1), IC302.32 (OB1), X302.4
E0_B12: C316.1, IC302.23 (OB2), IC302.24 (OB2), IC302.28 (OB2), IC302.29 (OB2), X302.3
GND: C301.2, C302.2, C303.2, C304.2, C307.2, C308.2, C309.2, C310.2, C311.2, C312.2, C313.2, C314.2, C315.2, C316.2, C317.-, C318.-, C319.2, C320.2, C321.-, C322.-, C323.2, C324.2, C326.2, C327.2, C328.2, C329.2, C330.2, C331.-, C332.2, C333.-, IC301.17 (GND), IC301.21 (CLK), IC301.39 (GND), IC301.43 (TST_MODE), IC301.44 (GND), IC302.17 (GND), IC302.21 (CLK), IC302.39 (GND), IC302.43 (TST_MODE), IC302.44 (GND), IC303.17 (GND), IC303.21 (CLK), IC303.39 (GND), IC303.43 (TST_MODE), IC303.44 (GND), R301.2, R302.2, R303.2, R304.2, R305.2, R306.2; also elsewhere on the board
MISO: IC301.14 (SDO), IC302.14 (SDO), IC303.14 (SDO); also elsewhere on the board
MOSI: IC301.15 (SDI), IC302.15 (SDI), IC303.15 (SDI); also elsewhere on the board
unnamed: C305.1, IC301.35 (VHS)
unnamed: IC301.9 (BRA), IC301.12 (SRA), R301.1
unnamed: IC301.22 (SRB), IC301.25 (BRB), R302.1
unnamed: C301.1, IC301.13 (5V_OUT)
unnamed: C325.1, IC303.35 (VHS)
unnamed: IC303.9 (BRA), IC303.12 (SRA), R305.1
unnamed: IC303.22 (SRB), IC303.25 (BRB), R306.1
unnamed: C323.1, IC303.13 (5V_OUT)
unnamed: C306.1, IC302.35 (VHS)
unnamed: IC302.9 (BRA), IC302.12 (SRA), R303.1
unnamed: IC302.22 (SRB), IC302.25 (BRB), R304.1
unnamed: C302.1, IC302.13 (5V_OUT)
SCK: IC301.16 (SCK), IC302.16 (SCK), IC303.16 (SCK); also elsewhere on the board
X_DIR: IC301.41 (DIR); also elsewhere on the board
X_SG_TST: IC301.38 (SG_TST); also elsewhere on the board
X_STP: IC301.42 (STEP); also elsewhere on the board
Y_DIR: IC303.41 (DIR); also elsewhere on the board
Y_SG_TST: IC303.38 (SG_TST); also elsewhere on the board
Y_STP: IC303.42 (STEP); also elsewhere on the board
Z_DIR: IC302.41 (DIR); also elsewhere on the board
Z_SG_TST: IC302.38 (SG_TST); also elsewhere on the board
Z_STP: IC302.42 (STEP); also elsewhere on the board

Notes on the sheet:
X- Y- Z-Axis

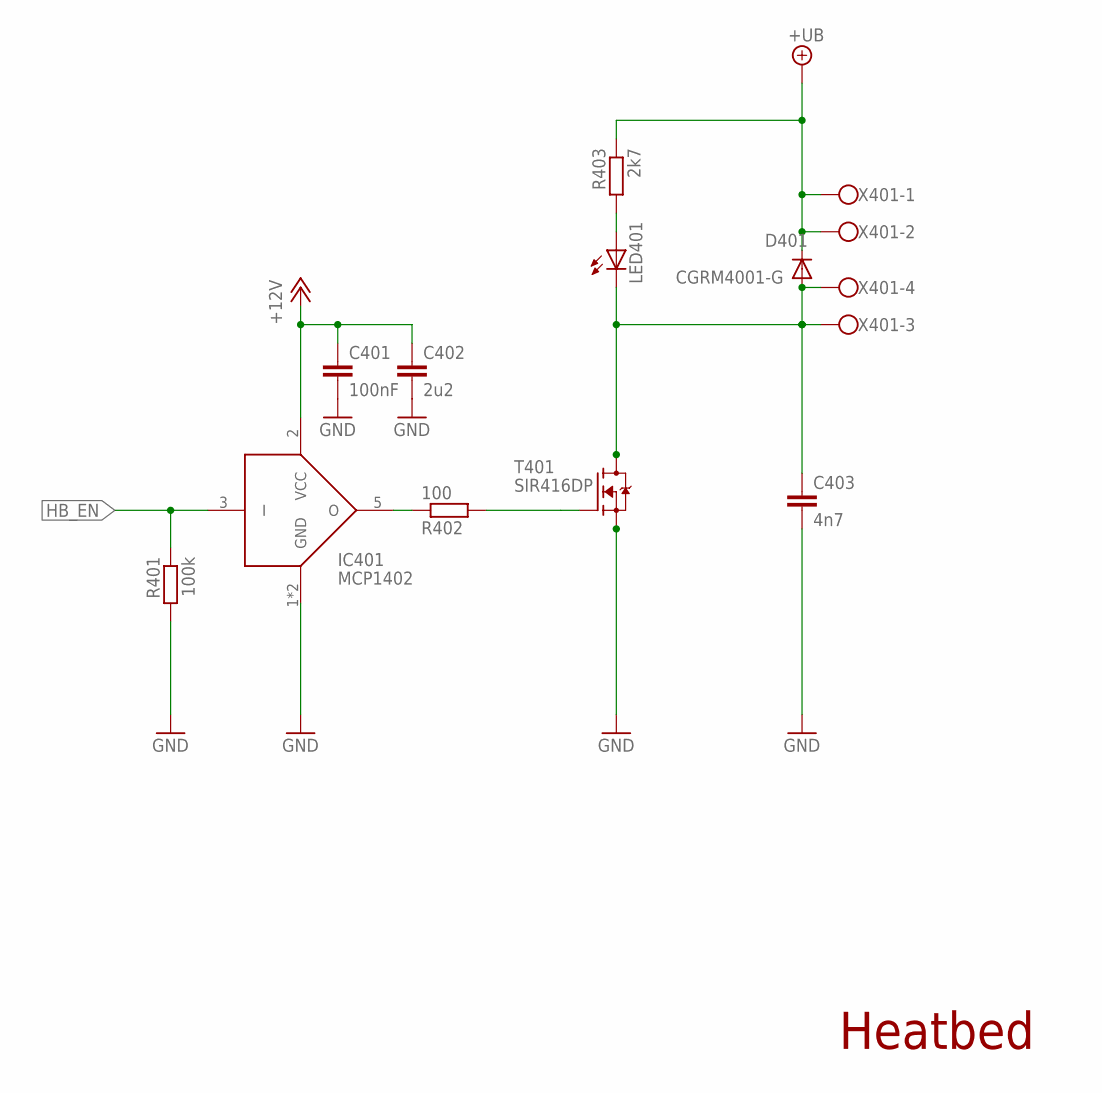
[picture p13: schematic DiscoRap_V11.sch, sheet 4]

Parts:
C401: 100nF; 0805
C402: 2u2; 0805
C403: 4n7; 0805
D401: CGRM4001-G; SOD-123_MINI-SMA
IC401: MCP1402; SOT23-5L
LED401: LEDCHIPLED_0805; CHIPLED_0805
R401: 100k; 0805
R402: 100; 0805
R403: 2k7; 0805
T401: SIR416DP; SO-8_POWERPACK
X401: W237-4

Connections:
+12V: C401.1, C402.1, IC401.2 (VCC); also elsewhere on the board
+UB: D401.C, R403.1, X401.1, X401.2; also elsewhere on the board
GND: C401.2, C402.2, C403.2, IC401.1 (GND), IC401.4 (GND), R401.2, T401.1 (S), T401.2 (S), T401.3 (S); also elsewhere on the board
HB_EN: IC401.3 (I), R401.1; also elsewhere on the board
unnamed: R402.2, T401.4 (G)
unnamed: IC401.5 (O), R402.1
unnamed: C403.1, D401.A, LED401.C, T401.5 (D), T401.6 (D), T401.7 (D), T401.8 (D), T401.EXP_PAD (D), X401.3, X401.4
unnamed: LED401.A, R403.2

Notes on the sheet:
Heatbed

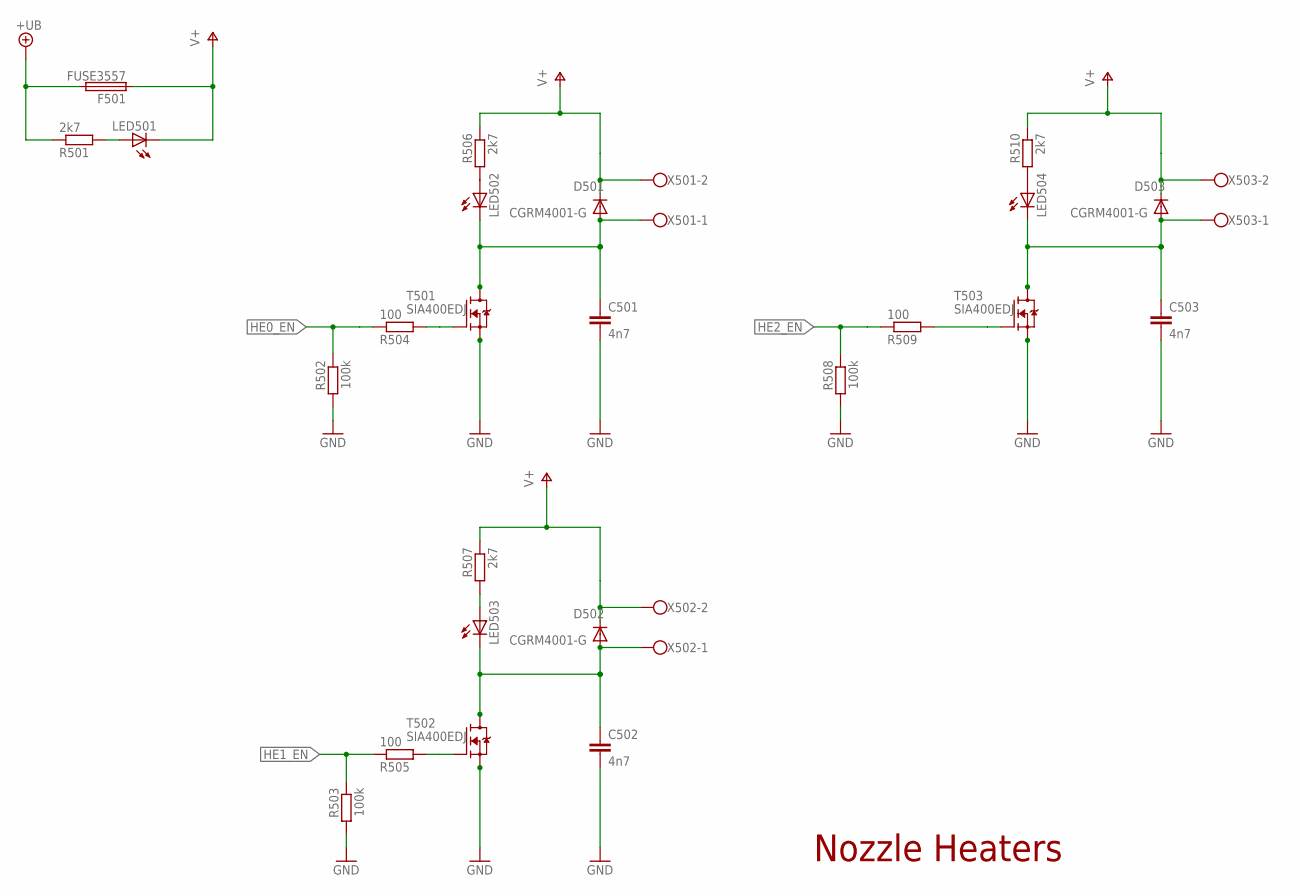
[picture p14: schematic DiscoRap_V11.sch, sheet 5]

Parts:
C501, C502, C503: 4n7; 0805
D501, D502, D503: CGRM4001-G; SOD-123_MINI-SMA
F501: FUSE3557; 3557
LED501, LED502, LED503, LED504: LEDCHIPLED_0805; CHIPLED_0805
R501, R506, R507, R510: 2k7; 0805
R502, R503, R508: 100k; 0805
R504, R505, R509: 100; 0805
T501, T502, T503: SIA400EDJ; SC70-6L
X501, X502, X503: W237-102

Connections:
+UB: F501.3 (2), F501.4 (2), R501.1; also elsewhere on the board
GND: C501.2, C502.2, C503.2, R502.2, R503.2, R508.2, T501.4 (S), T501.EXP_SOURCE (S), T502.4 (S), T502.EXP_SOURCE (S), T503.4 (S), T503.EXP_SOURCE (S); also elsewhere on the board
HE0_EN: R502.1, R504.1; also elsewhere on the board
HE1_EN: R503.1, R505.1; also elsewhere on the board
HE2_EN: R508.1, R509.1; also elsewhere on the board
unnamed: R504.2, T501.3 (G)
unnamed: C501.1, D501.A, LED502.C, T501.1 (D), T501.2 (D), T501.5 (D), T501.6 (D), T501.EXP_DRAIN (D), X501.1
unnamed: LED502.A, R506.2
unnamed: R505.2, T502.3 (G)
unnamed: C502.1, D502.A, LED503.C, T502.1 (D), T502.2 (D), T502.5 (D), T502.6 (D), T502.EXP_DRAIN (D), X502.1
unnamed: LED503.A, R507.2
unnamed: R509.2, T503.3 (G)
unnamed: C503.1, D503.A, LED504.C, T503.1 (D), T503.2 (D), T503.5 (D), T503.6 (D), T503.EXP_DRAIN (D), X503.1
unnamed: LED504.A, R510.2
unnamed: LED501.A, R501.2
V+: D501.C, D502.C, D503.C, F501.1, F501.2 (1), LED501.C, R506.1, R507.1, R510.1, X501.2, X502.2, X503.2

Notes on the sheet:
Nozzle Heaters

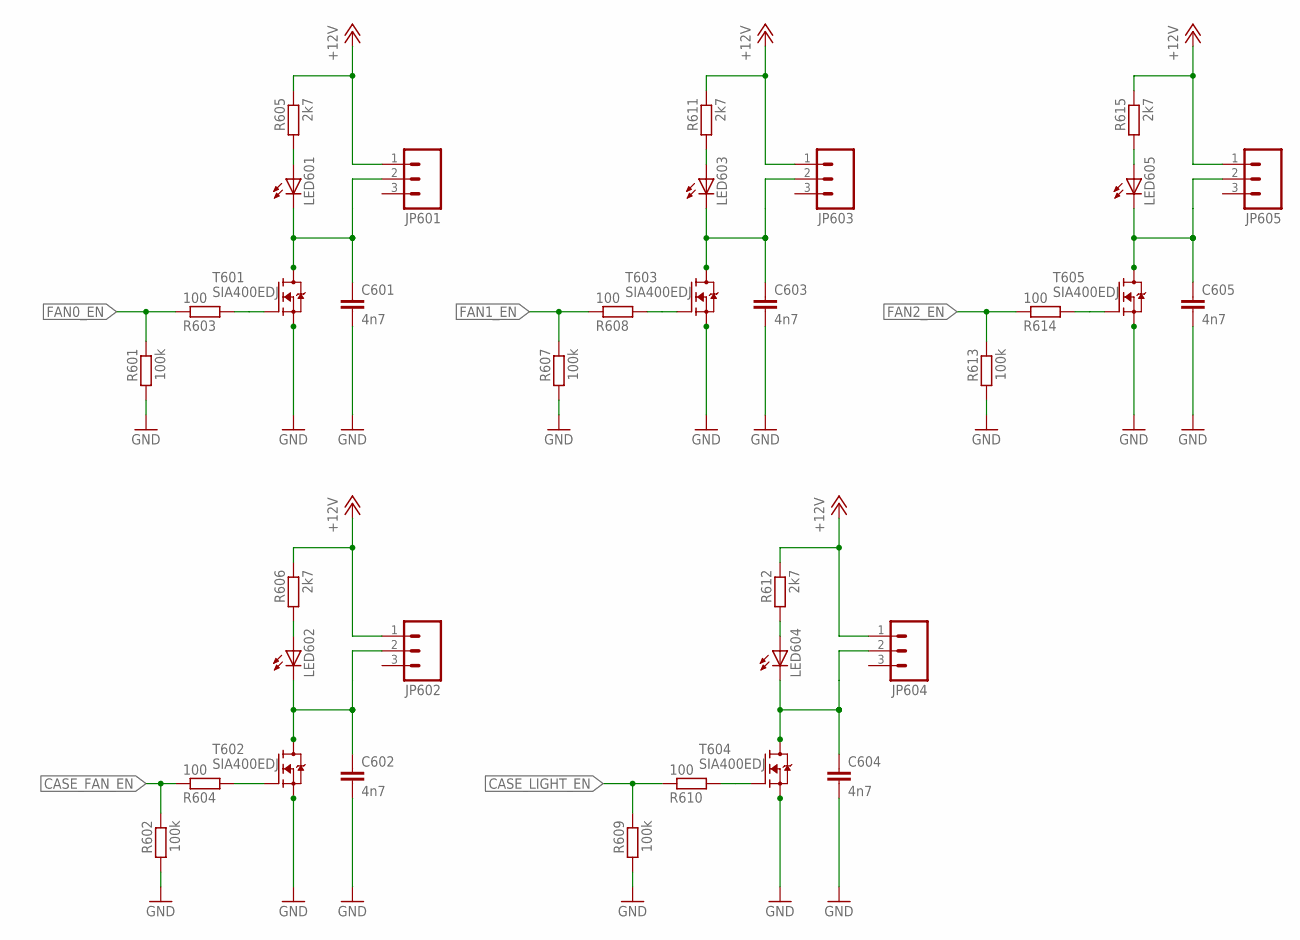
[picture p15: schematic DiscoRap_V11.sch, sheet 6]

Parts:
C601, C602, C603, C604, C605: 4n7; 0805
JP601, JP602, JP603, JP604, JP605: M03POLAR; MOLEX-1X3
LED601, LED602, LED603, LED604, LED605: LEDCHIPLED_0805; CHIPLED_0805
R601, R602, R607, R609, R613: 100k; 0805
R603, R604, R608, R610, R614: 100; 0805
R605, R606, R611, R612, R615: 2k7; 0805
T601, T602, T603, T604, T605: SIA400EDJ; SC70-6L

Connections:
+12V: JP601.1, JP602.1, JP603.1, JP604.1, JP605.1, R605.1, R606.1, R611.1, R612.1, R615.1; also elsewhere on the board
CASE_FAN_EN: R602.1, R604.1; also elsewhere on the board
CASE_LIGHT_EN: R609.1, R610.1; also elsewhere on the board
FAN0_EN: R601.1, R603.1; also elsewhere on the board
FAN1_EN: R607.1, R608.1; also elsewhere on the board
FAN2_EN: R613.1, R614.1; also elsewhere on the board
GND: C601.2, C602.2, C603.2, C604.2, C605.2, R601.2, R602.2, R607.2, R609.2, R613.2, T601.4 (S), T601.EXP_SOURCE (S), T602.4 (S), T602.EXP_SOURCE (S), T603.4 (S), T603.EXP_SOURCE (S), T604.4 (S), T604.EXP_SOURCE (S), T605.4 (S), T605.EXP_SOURCE (S); also elsewhere on the board
unnamed: R603.2, T601.3 (G)
unnamed: C601.1, JP601.2, LED601.C, T601.1 (D), T601.2 (D), T601.5 (D), T601.6 (D), T601.EXP_DRAIN (D)
unnamed: LED601.A, R605.2
unnamed: R608.2, T603.3 (G)
unnamed: C603.1, JP603.2, LED603.C, T603.1 (D), T603.2 (D), T603.5 (D), T603.6 (D), T603.EXP_DRAIN (D)
unnamed: LED603.A, R611.2
unnamed: R614.2, T605.3 (G)
unnamed: C605.1, JP605.2, LED605.C, T605.1 (D), T605.2 (D), T605.5 (D), T605.6 (D), T605.EXP_DRAIN (D)
unnamed: LED605.A, R615.2
unnamed: R604.2, T602.3 (G)
unnamed: C602.1, JP602.2, LED602.C, T602.1 (D), T602.2 (D), T602.5 (D), T602.6 (D), T602.EXP_DRAIN (D)
unnamed: LED602.A, R606.2
unnamed: R610.2, T604.3 (G)
unnamed: C604.1, JP604.2, LED604.C, T604.1 (D), T604.2 (D), T604.5 (D), T604.6 (D), T604.EXP_DRAIN (D)
unnamed: LED604.A, R612.2

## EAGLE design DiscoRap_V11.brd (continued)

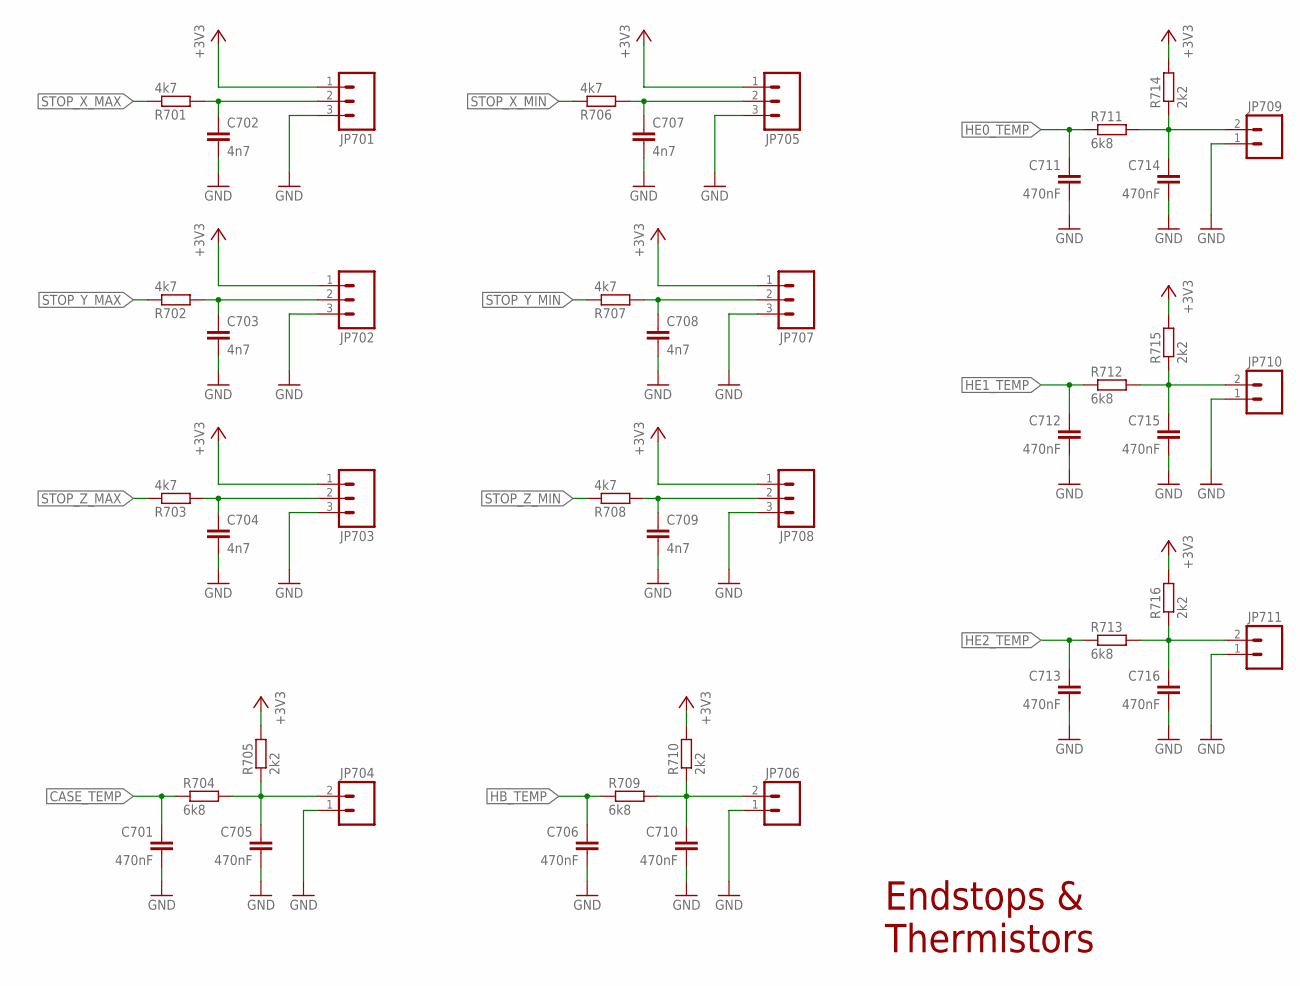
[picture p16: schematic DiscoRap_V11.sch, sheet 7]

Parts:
C701, C705, C706, C710, C711, C712, C713, C714, C715, C716: 470nF; 0805
C702, C703, C704, C707, C708, C709: 4n7; 0805
JP701, JP702, JP703, JP705, JP707, JP708: M03POLAR; MOLEX-1X3
JP704, JP706, JP709, JP710, JP711: M02POLAR; MOLEX-1X2
R701, R702, R703, R706, R707, R708: 4k7; 0805
R704, R709, R711, R712, R713: 6k8; 0805
R705, R710, R714, R715, R716: 2k2; 0805

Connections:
+3V3: JP701.1, JP702.1, JP703.1, JP705.1, JP707.1, JP708.1, R705.2, R710.2, R714.2, R715.2, R716.2; also elsewhere on the board
CASE_TEMP: C701.1, R704.1; also elsewhere on the board
GND: C701.2, C702.2, C703.2, C704.2, C705.2, C706.2, C707.2, C708.2, C709.2, C710.2, C711.2, C712.2, C713.2, C714.2, C715.2, C716.2, JP701.3, JP702.3, JP703.3, JP704.1, JP705.3, JP706.1, JP707.3, JP708.3, JP709.1, JP710.1, JP711.1; also elsewhere on the board
HB_TEMP: C706.1, R709.1; also elsewhere on the board
HE0_TEMP: C711.1, R711.1; also elsewhere on the board
HE1_TEMP: C712.1, R712.1; also elsewhere on the board
HE2_TEMP: C713.1, R713.1; also elsewhere on the board
unnamed: C702.1, JP701.2, R701.2
unnamed: C703.1, JP702.2, R702.2
unnamed: C704.1, JP703.2, R703.2
unnamed: C709.1, JP708.2, R708.2
unnamed: C708.1, JP707.2, R707.2
unnamed: C707.1, JP705.2, R706.2
unnamed: C710.1, JP706.2, R709.2, R710.1
unnamed: C714.1, JP709.2, R711.2, R714.1
unnamed: C715.1, JP710.2, R712.2, R715.1
unnamed: C716.1, JP711.2, R713.2, R716.1
unnamed: C705.1, JP704.2, R704.2, R705.1
STOP_X_MAX: R701.1; also elsewhere on the board
STOP_X_MIN: R706.1; also elsewhere on the board
STOP_Y_MAX: R702.1; also elsewhere on the board
STOP_Y_MIN: R707.1; also elsewhere on the board
STOP_Z_MAX: R703.1; also elsewhere on the board
STOP_Z_MIN: R708.1; also elsewhere on the board

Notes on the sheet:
Endstops & Thermistors

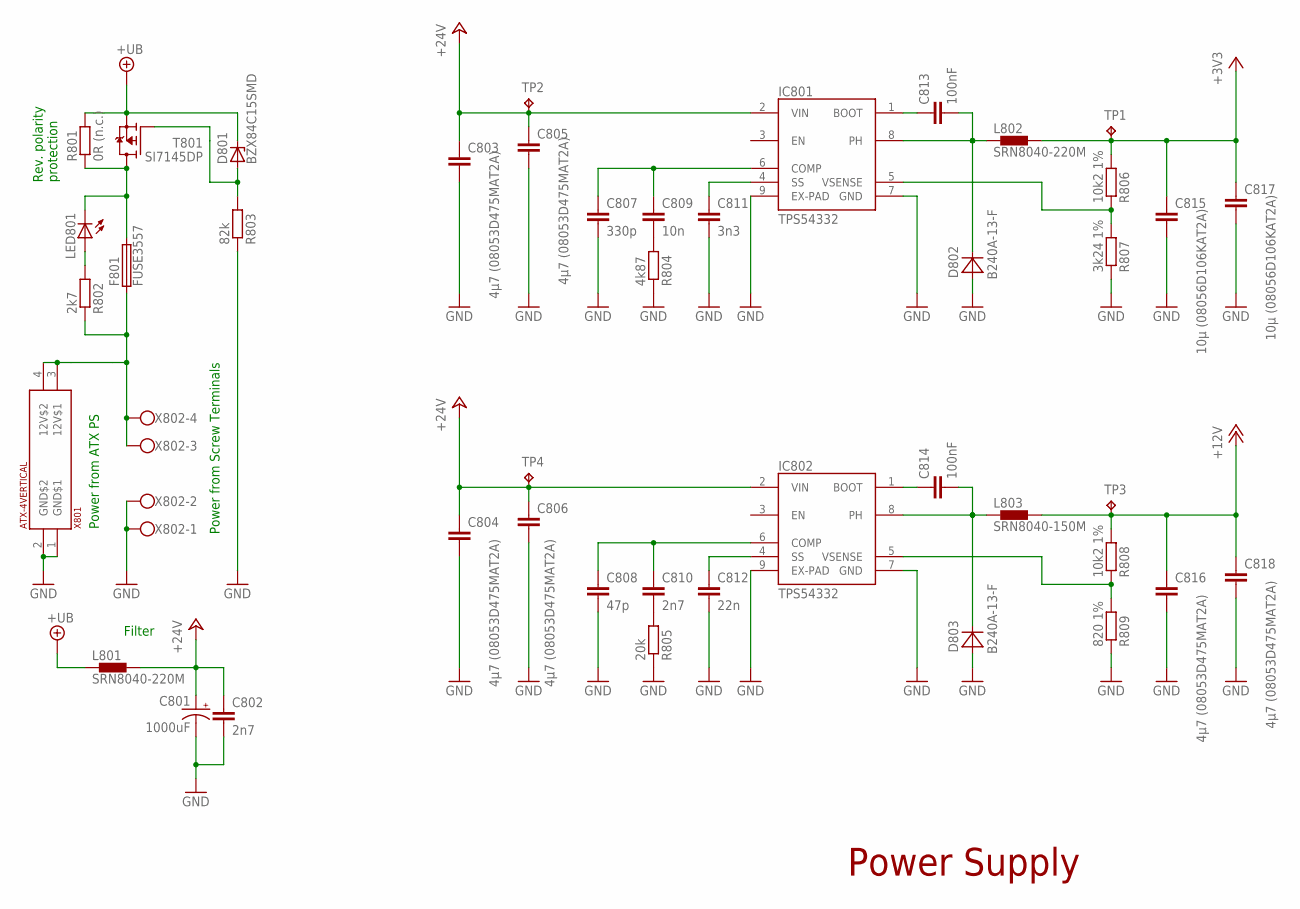
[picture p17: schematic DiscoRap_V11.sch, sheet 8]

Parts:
C801: 1000uF; CPOL-RADIAL-1000UF-25V
C802, C810: 2n7; 0805
C803, C804, C805, C806, C816, C818: 4µ7 (08053D475MAT2A); 0805
C807: 330p; 0805
C808: 47p; 0805
C809: 10n; 0805
C811: 3n3; 0805
C812: 22n; 0805
C813, C814: 100nF; 0805
C815, C817: 10µ (08056D106KAT2A); 0805
D801: BZX84C15SMD; TO236
D802, D803: B240A-13-F; SMA
F801: FUSE3557; 3557
IC801, IC802: TPS54332; PDSO-G8
L801, L802: SRN8040-220M; SRN8040
L803: SRN8040-150M; SRN8040
LED801: LEDCHIPLED_0805; CHIPLED_0805
R801: 0R (n.c.); R2512
R802: 2k7; 0805
R803: 82k; 0805
R804: 4k87; 0805
R805: 20k; 0805
R806, R808: 10k2 1%; 0805
R807: 3k24 1%; 0805
R809: 820 1%; 0805
T801: SI7145DP; SO-8_POWERPACK
TP1, TP2, TP3, TP4: TPB1,27; B1,27
X801: ATX-4VERTICAL; MINIFITJR-4-VERTICAL
X802: W237-4

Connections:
+3V3: C815.1, C817.1, L802.2, R806.2, TP1.TP; also elsewhere on the board
+12V: C816.1, C818.1, L803.2, R808.2, TP3.TP; also elsewhere on the board
+24V: C801.1 (+), C802.1, C803.1, C804.1, C805.1, C806.1, IC801.2 (VIN), IC802.2 (VIN), L801.2, TP2.TP, TP4.TP
+UB: D801.C, L801.1, R801.2, T801.1 (S), T801.2 (S), T801.3 (S); also elsewhere on the board
GND: C801.2 (-), C802.2, C803.2, C804.2, C805.2, C806.2, C807.2, C808.2, C811.2, C812.2, C815.2, C816.2, C817.2, C818.2, D802.A, D803.A, IC801.7 (GND), IC801.9 (EX-PAD), IC802.7 (GND), IC802.9 (EX-PAD), R803.1, R804.1, R805.1, R807.1, R809.1, X801.1 (GND$1), X801.2 (GND$2), X802.1, X802.2; also elsewhere on the board
unnamed: C809.2, R804.2
unnamed: C811.1, IC801.4 (SS)
unnamed: C813.1, IC801.1 (BOOT)
unnamed: C814.2, D803.C, IC802.8 (PH), L803.1
unnamed: IC802.5 (VSENSE), R808.1, R809.2
unnamed: C808.1, C810.1, IC802.6 (COMP)
unnamed: C810.2, R805.2
unnamed: C812.1, IC802.4 (SS)
unnamed: C814.1, IC802.1 (BOOT)
unnamed: C813.2, D802.C, IC801.8 (PH), L802.1
unnamed: IC801.5 (VSENSE), R806.1, R807.2
unnamed: C807.1, C809.1, IC801.6 (COMP)
unnamed: D801.A, R803.2, T801.4 (G)
unnamed: F801.1, F801.2 (1), R802.1, X801.3 (12V$1), X801.4 (12V$2), X802.3, X802.4
unnamed: F801.3 (2), F801.4 (2), LED801.C, R801.1, T801.5 (D), T801.6 (D), T801.7 (D), T801.8 (D), T801.EXP_PAD (D)
unnamed: LED801.A, R802.2

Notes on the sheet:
Power Supply
Power from ATX PS
Power from Screw Terminals
Rev. polarity protection
Filter

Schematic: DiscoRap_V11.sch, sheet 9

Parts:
H901, H902, H903, H904: MOUNT-HOLE3.2; 3,2
JP901: PINHD-2X3; 2X03
JP902: M02POLAR; MOLEX-1X2
R901, R902, R903: 3k3; 0805

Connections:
+3V3: JP901.2; also elsewhere on the board
AUX_IN_0: JP901.1; also elsewhere on the board
AUX_IN_1: JP901.3; also elsewhere on the board
AUX_IN_2: JP901.5; also elsewhere on the board
EMERGENCY_STOP: JP902.2; also elsewhere on the board
GND: JP901.4, JP901.6, JP902.1, R901.1, R902.1, R903.1; also elsewhere on the board
MISO: R901.2; also elsewhere on the board
MOSI: R902.2; also elsewhere on the board
SCK: R903.2; also elsewhere on the board

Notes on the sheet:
Other

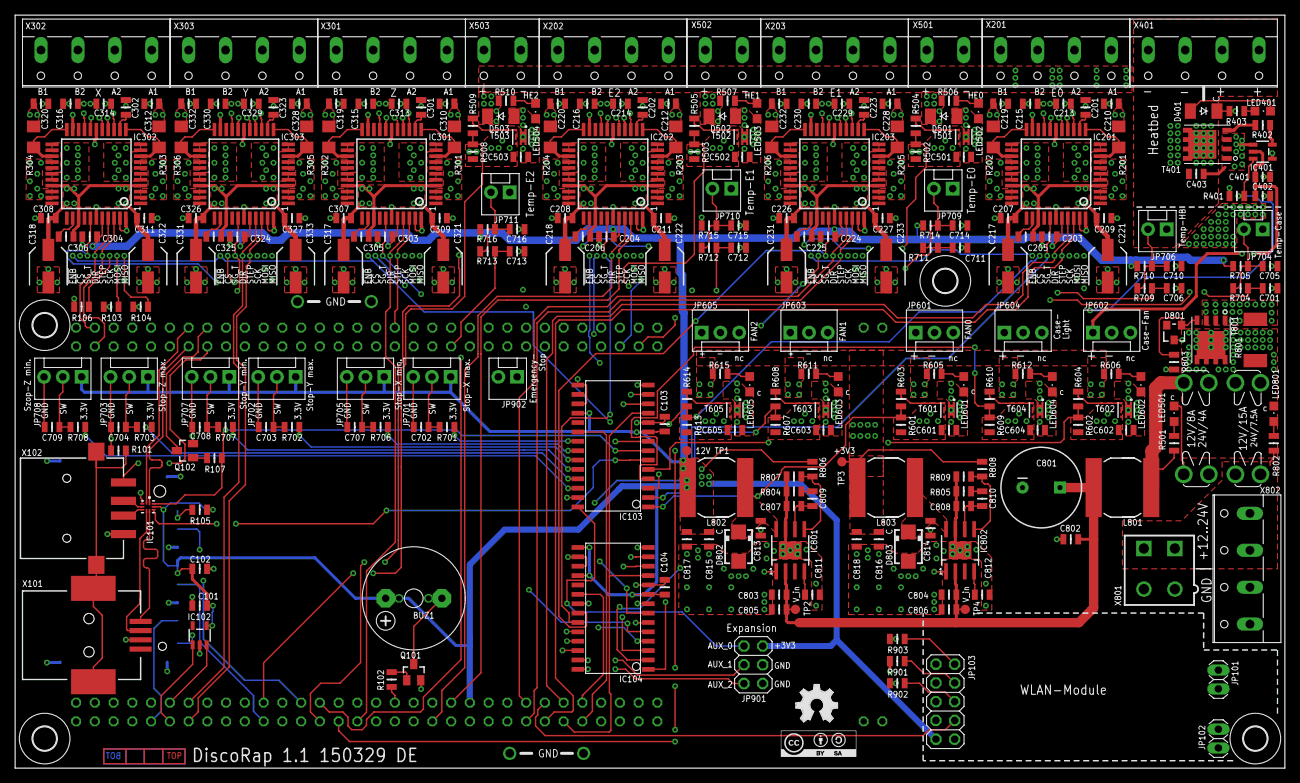
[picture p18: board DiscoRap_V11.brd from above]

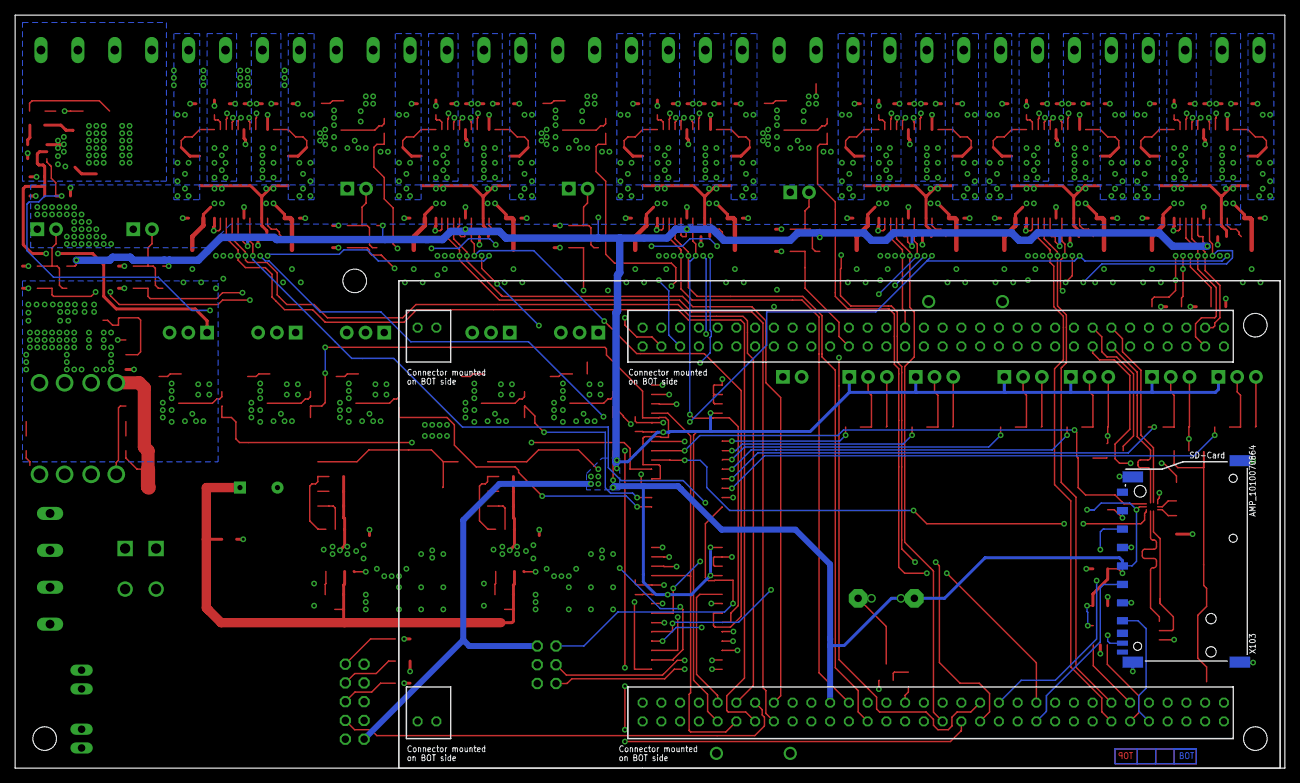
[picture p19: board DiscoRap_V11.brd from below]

Board: 4 copper layers, 172.0 x 102.0 mm, 286 parts (2 on the bottom side), 190 nets.

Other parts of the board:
LOGO1: OSHW_LOGO_FILLX0200-NT; OSHW_FILLX200_NOTEXT
U$3: CC-BY-SA

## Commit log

2015-04-05 DiscoveRap initial PCB Version
    [DiscoRap_V11.sch]
2015-04-05 DiscoveRap initial PCB release
    [DiscoRap_V11.brd]
2015-04-05 BOM for DiscoveRap
    [DiscoRap_V11_BOM.xlsx]
2015-04-15 Add schematics in pdf format
